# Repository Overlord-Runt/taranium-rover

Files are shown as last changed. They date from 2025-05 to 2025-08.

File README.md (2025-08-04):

# Taranium Rover
Made By Overlord Runt // Taran The Idiot

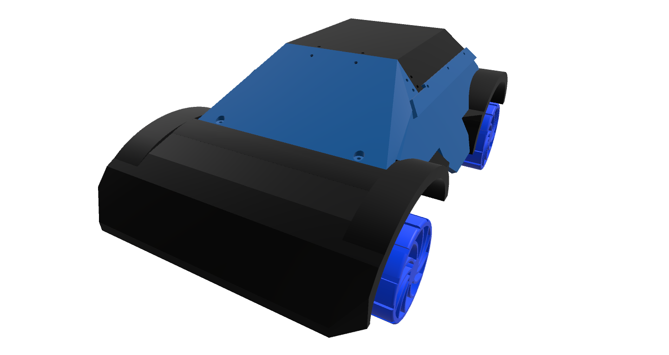
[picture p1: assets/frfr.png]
dksjfksd


## Taranium Rover
This is an RC car I made for Hack Club's [Highway](https://highway.hackclub.com). It has a 4WD system and can turn with all 4 wheels. It uses ESP32 and ESPNow to communicate between the car and the controller

## The Car

dsf

### CAD
Majority of this project was getting the cadding of all the different parts done. This isnt what normal custom RC Cars look like and thats because everyone uses the exact same optimal design but I want to make and design something myself. idrc about the "optimal way" cuz where is the fun in that.

This thing is really big so you need like a lot of plates if you want to build it. Roughly about 6 plates and 40 hours of non stop printing.

It uses a crap ton of M3 screws and heatsets, so make sure you stock up on those

### Engineering
So bunch of enginnering went into this design. First the turning system. the 2 front wheels turn separately to allow for differential steering and reduced drag. It also allows me to use weaker and smaller 9g servos that are able to turn one wheel, but not 2.\
It used steel dowels to hold the pieces together and to ensure minimal friction between parts(make it turn stronger)

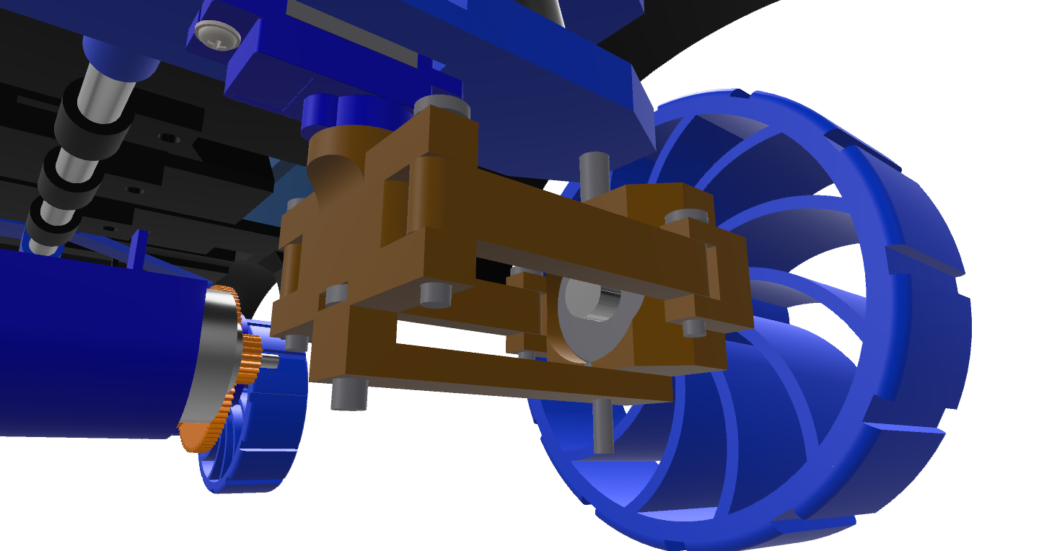
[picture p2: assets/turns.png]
fgd


The bottom piece is there for stability and to make sure the wheel mount doesnt collapse.\
The suspensions are a bunch of high strendth springs that help distribute the weight of the whole car evenly through the wheels and absorb large bumps.\
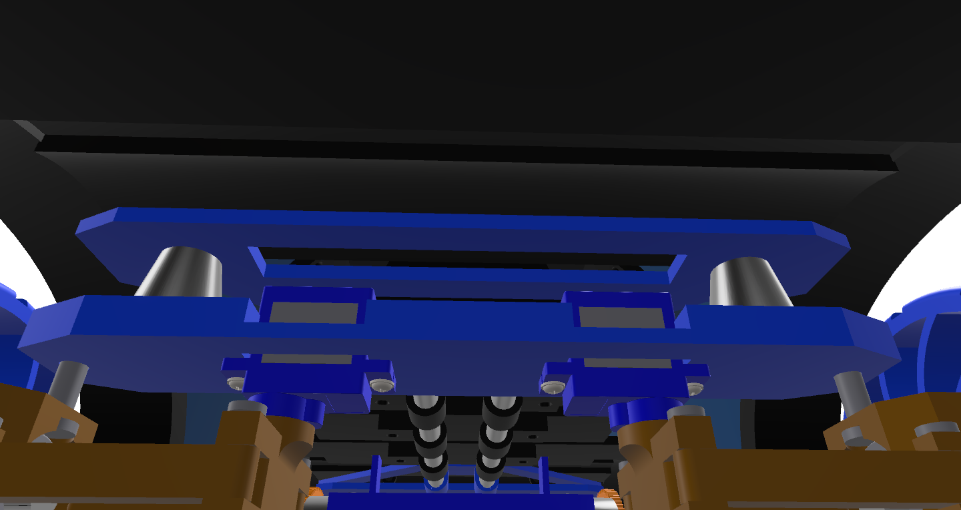
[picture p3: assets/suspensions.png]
dafs
\
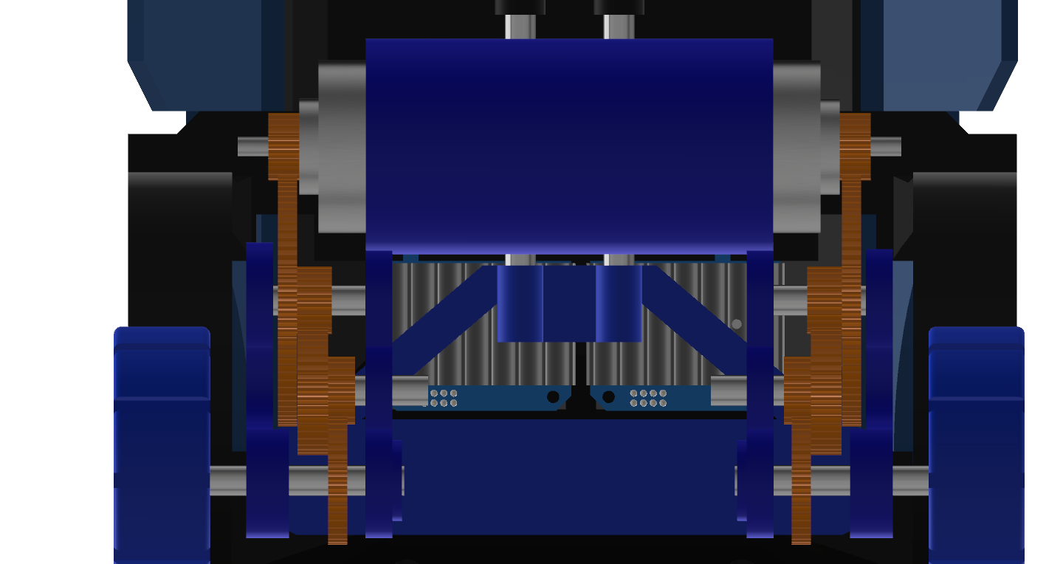
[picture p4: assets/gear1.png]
dfsdf


The gear system uses a 16:1 gear down from the 12 000 rpm motor to give a 750 rpm spin under no load with roughly 6-10 Kgcm torque. under load it will have about 4-500 rpm and go about 1m/s. I use a large amount of bearings and steel rods in this design. For assembly, use a grinder to chop the steel rods into all the different lengths needed. You can refer to Full-Build.step in the CAD folder to see how everything is put together.

### PCB / Wiring Diagrams
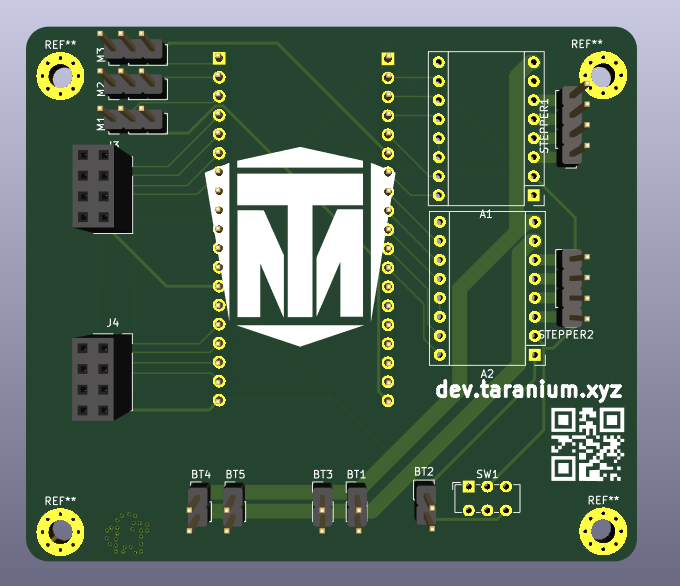
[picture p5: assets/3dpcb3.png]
sda


The PCB didnt really take too long but I did have to make many different revisions to get here that did end up taking a lot of time.\
I wanted this to be somewhat of a universal mainboard that could be used in multiple use cases. Which is why I included space for stepper motor drivers. specifically the A4988. as well as 3 places for servos

The PCB features 2 BTS7960 motor drivers. They have 8 pins that connect to the boards(mounted externally). The mainboard also has space to use A4988 stepper motor drivers if you wish to swap out the 775s for stepper motors. 

I didnt have a footprint for the esp32 board that I am using so I just used 2 header pins and separated them the distance that it said on the datasheet.

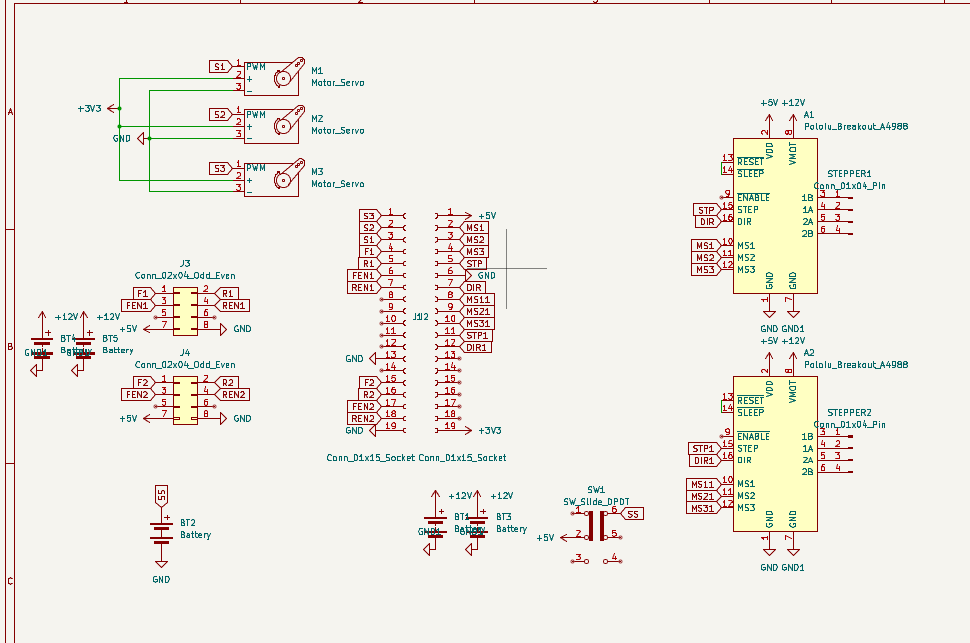
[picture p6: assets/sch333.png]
asd


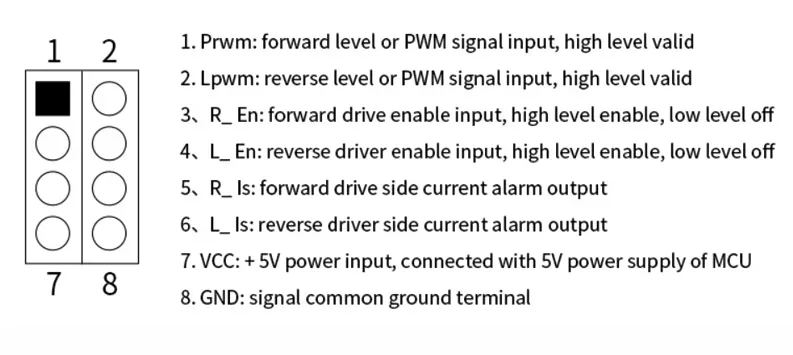
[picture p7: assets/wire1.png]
fadsf


this is the pinout for the Motor driver. it mathces that on the pcb so its an easy connection there

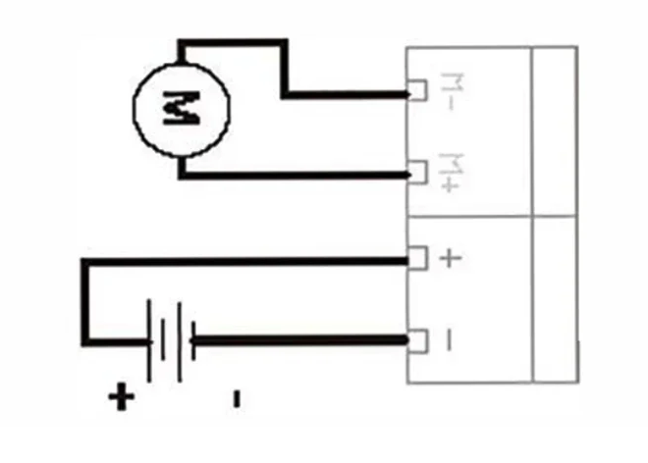
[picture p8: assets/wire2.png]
sdgfgsg


This is how you connect the motor driver to the battery and to the motor.

## The Controller
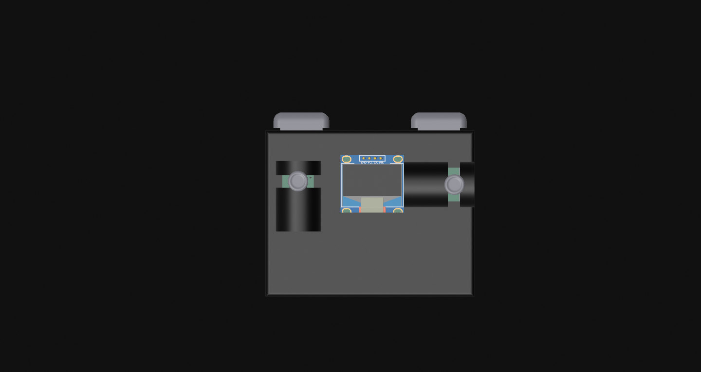
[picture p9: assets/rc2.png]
sdfs

### CAD
The controller was fairly easy to cad. it uses M3 screws to hold itself together.

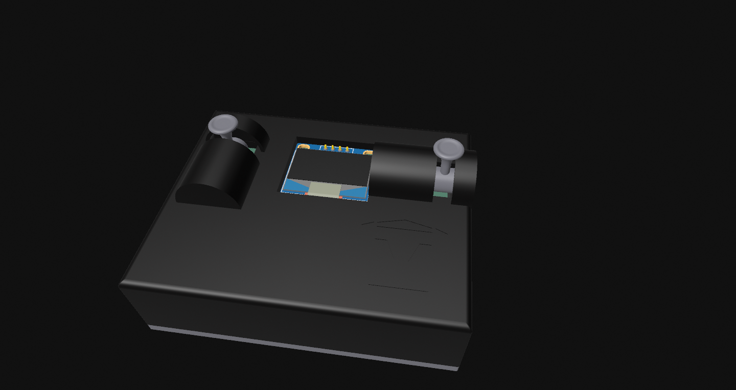
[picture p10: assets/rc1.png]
fs


The triggers are just extensions to the buttons with a small indent to act as a stabiliser

The joysticks/encoder rods are cool in that I didn't use the revolve tool to make them. just a bunch of extrusions, drafts, and fillets.

Then in order to make it actually buildable, i chopped off the end and added a dowel

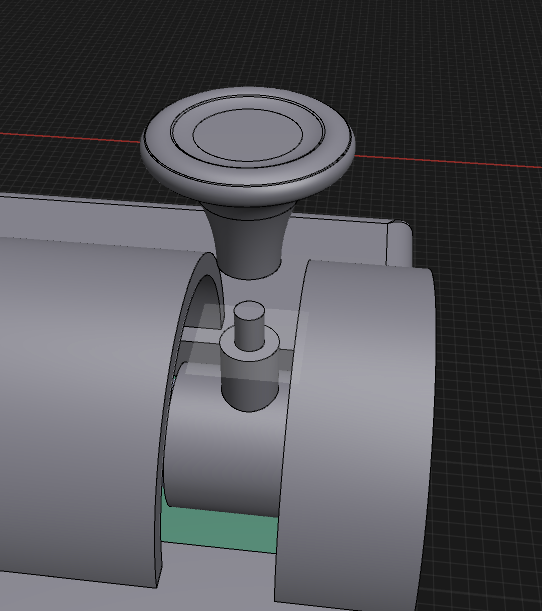
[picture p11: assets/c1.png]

### PCB
For the pcb I wanted to keep it basic. So 2 encoders. One for speed, other for turning. then 2 buttons. one to reverse, other for anything else you might wanna add in the future.\
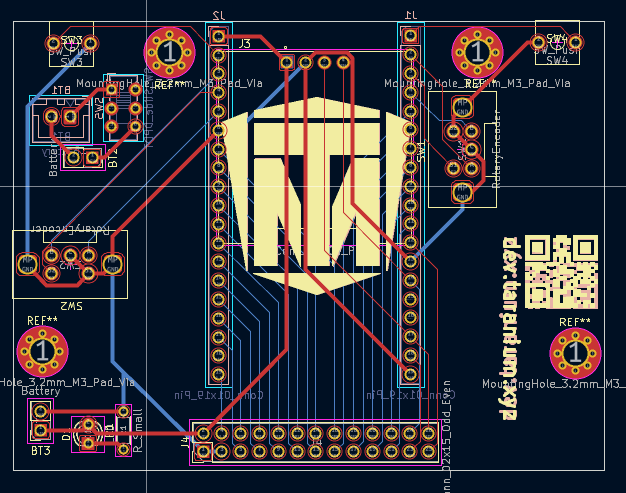
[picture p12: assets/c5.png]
\
Its a cool design if you ask me and it does its job.\
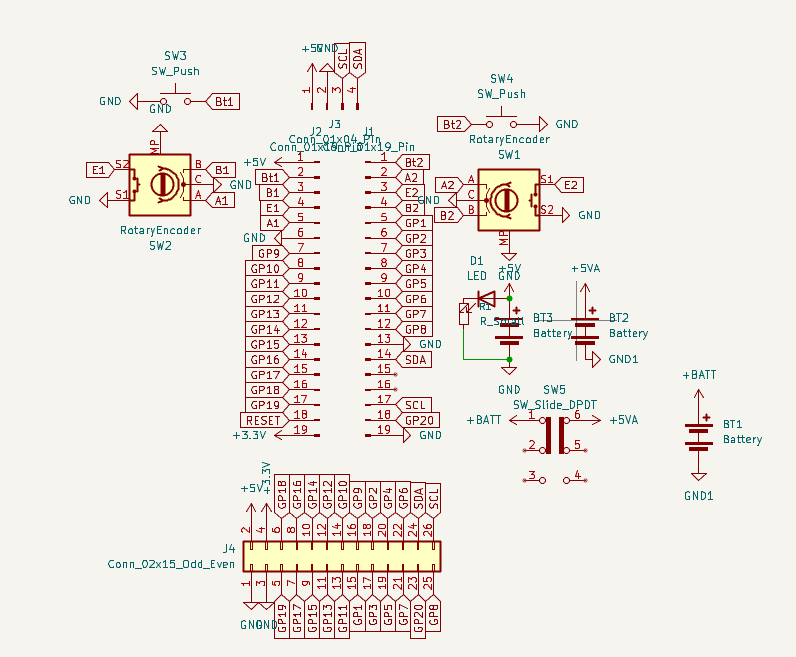
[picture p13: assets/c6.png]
sdad


## Firmware

uses espnow and you can find the firmware in the firmware folders. the names should tell you all you need to knwo about which on goes to which but for those who are a little slow, controller.ino flashes to the controller and mainboard.ino flashes to the mainboard

## How To Build

1. Print out all parts
2. Insert heatsets into all parts
3. Solder circuit boards as shown in schematics
4. assemble internal structures such as the turning system
5. Slide connectors onto rods then use rods to connect 2 internals sides
6. Attach chasis frames beginning with the parts that connect to the frame.
7. Flash esp with code
8. mount pcb of top panel
9. insert battery and sercure it down with screws
10. screw on top panels
11. flash controller with code
12. solder pcb
13. attach first part of the sticks to encoders
14. mount pcb to case
15. attach second part of sticks to encoders and use super glue or hot glue to hold it down
16. screw back panel
17. play enjoy.

If i forgot something I will add it on when I build

## BOM

|Name|QTY|Cost(AUD)|Cost(USD)|Link|
|----|---|---|---|----|
|3s 2.2AH LiPo|1|$47.19||[LINK](https://www.amazon.com.au/gp/product/B09NXM2DW4/ref=sw_img_1?smid=A3S3YJCXW342CA&psc=1)|
|ESP32 Dev Board|2|$7.39||[LINK](https://www.aliexpress.com/item/1005008499671222.html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)|
|Buck Converter|1|$1.47||[LINK](https://www.aliexpress.com/item/1005006365697021.html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)|
|Steel Rods|1|$13.59||[LINK](https://www.aliexpress.com/item/1005005041338002.html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)|
|775 12V DC Motor|2|$31.40|20.2|[LINK](https://www.aliexpress.com/item/1005006573459459.html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)|
|BTS7960 Motor Driver|2|$15.00|9.65|[LINK](https://www.aliexpress.com/item/1005007091280016.html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)|
|Header Pins|1|$2.54||[LINK](https://www.aliexpress.com/item/1005006034877497.html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)|
|Servo Motor 5V|2|$4.69||[LINK](https://www.aliexpress.com/item/1005006572297006.html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)|
|M3x10mm Screws||$2.82||[LINK](https://www.aliexpress.com/item/32810852732.html?spm=a2g0o.order_list.order_list_main.28.74441802cg1DM1)|
|M3x16mm Screws||$3.43||[LINK](https://www.aliexpress.com/item/32810852732.html?spm=a2g0o.order_list.order_list_main.28.74441802cg1DM1)|
|M3x6mm Screws||$2.29||[LINK](https://www.aliexpress.com/item/32810852732.html?spm=a2g0o.order_list.order_list_main.28.74441802cg1DM1)|
|M3D5L6 Heatsets|45|$3.82||[LINK](https://www.aliexpress.com/item/1005003582355741.html?spm=a2g0o.order_list.order_list_main.45.21221802z3BMxP)|
|M3 Steel Dowels 20mm|4|$2.47||[LINK](https://www.aliexpress.com/item/1005003990055624.html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)|
|M3 Steel Dowels 12mm|2|$2.41||[LINK](https://www.aliexpress.com/item/1005003990055624.html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)|
|M4 Steel Dowels 12mm|2|$2.47||[LINK](https://www.aliexpress.com/item/1005003990055624.html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)|
|M5 Steel Dowels 25mm|2|$3.16||[LINK](https://www.aliexpress.com/item/1005003990055624.html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)|
|Car Mainboard|1|9.18|$6.90|JLCPCB|
|Controller Board|1|15.1|$9.87|JLCPCB|
|3d Printed parts||||I aint counting how many there are|
|LiPo Balance Charger|1|$23.95||[LINK](https://www.amazon.com.au/Jinming-Battery-Balance-Charger-Blaster/dp/B07JDG4D8W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)|
|Horizontal Rotary Encoder|2|$4.90||[LINK](https://www.aliexpress.com/item/1005006128388016.html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)|
|T-plug connector|1|$2.61||[LINK](https://www.aliexpress.com/item/4001212535096.html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)|
|10 gauge wire|2m|$15.45||[LINK](https://www.aliexpress.com/item/1005007759043423.html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)|
|3.7V lipo|1|$14.99||[LINK](https://www.amazon.com.au/gp/product/B09R7F1VV5/ref=sw_img_1?smid=A12788XRWB37UE&th=1)|
|XH 2.54 Male connector|1|$1.79||[LINK](https://www.aliexpress.com/item/1005007460897865.html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)|
|6mm switch|2|$2.89||[LINK](https://www.aliexpress.com/item/1005004971266223.html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)|
|Hardened Springs|4|||sourced from my dad|
|1kg PLA|1||||
|1kg PETG|1||||
|Boost Converter|1|$4.83||[LINK](https://www.aliexpress.com/item/1005008447199869.html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)|
|SSD1306 128x64 OLED Display|1|$4.20||[LINK](https://www.aliexpress.com/item/1005009243034318.html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)|
|TOTAL||$246.03|$161.03||

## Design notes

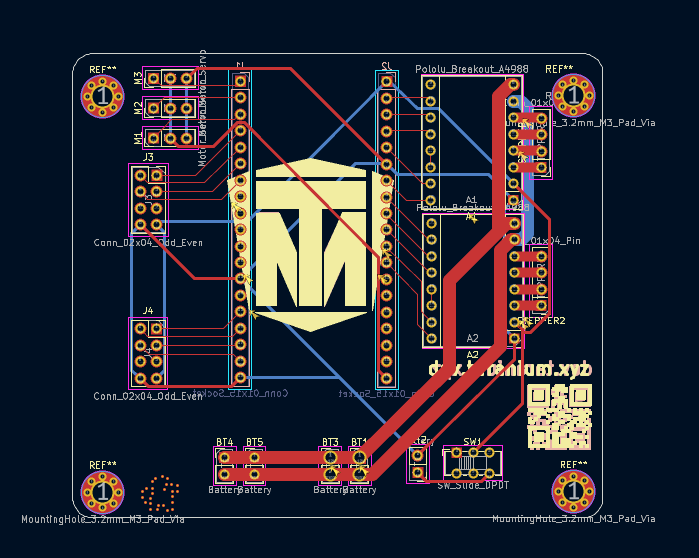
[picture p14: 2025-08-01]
assets/pcb333.png

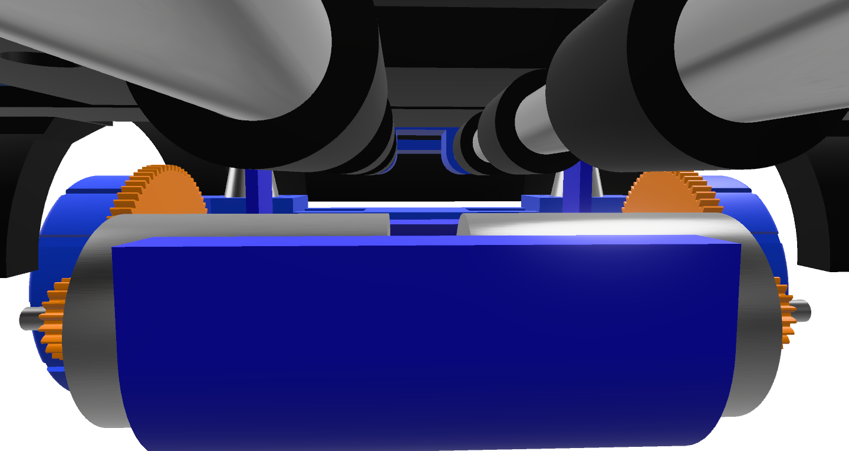
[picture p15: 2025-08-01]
assets/mots.png

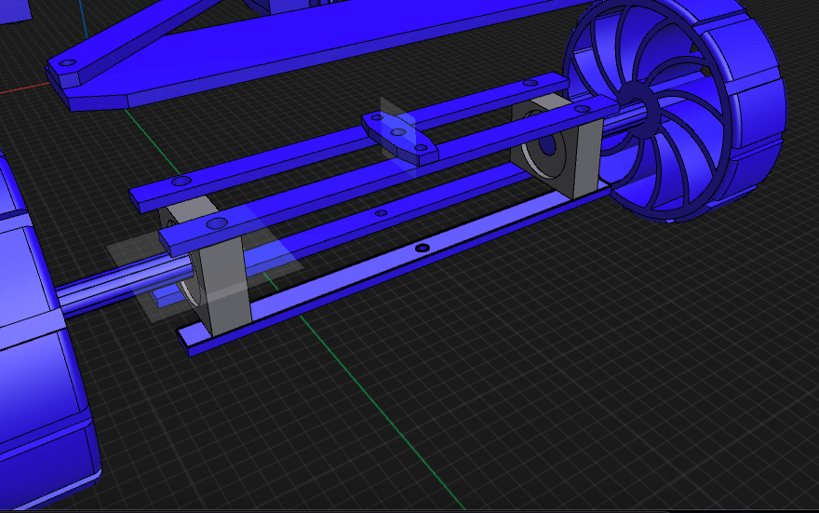
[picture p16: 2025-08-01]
assets/turn2.png

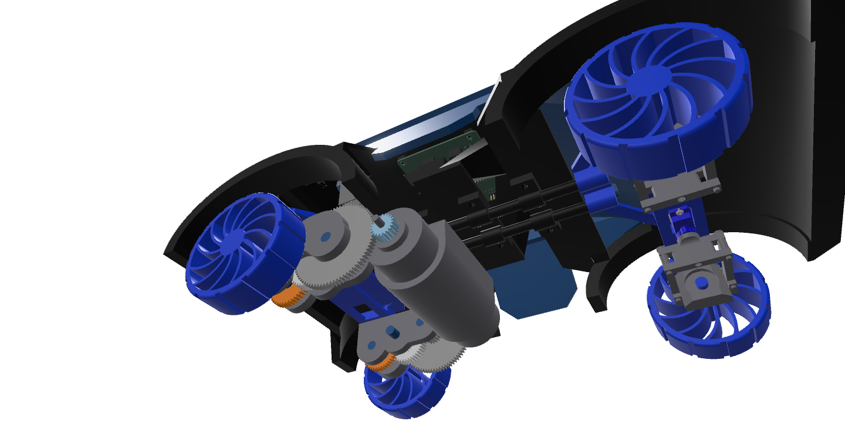
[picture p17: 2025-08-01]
assets/internals.png

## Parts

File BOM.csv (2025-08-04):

Name | QTY | Cost(AUD) | Cost(USD) | Link
3s 2.2AH LiPo | 1 | $47.19 |  | https://www.amazon.com.au/gp/product/B09NXM2DW4/ref=sw_img_1?smid=A3S3YJCXW342CA&psc=1
ESP32 Dev Board | 2 | $7.39 |  | https://www.aliexpress.com/item/1005008499671222.html?mp=1
Buck Converter | 1 | $1.47 |  | https://www.aliexpress.com/item/1005006365697021.html?mp=1
Steel Rods | 1 | $13.59 |  | https://www.aliexpress.com/item/1005005041338002.html?mp=1
775 12V DC Motor | 2 | $31.40 | 20.2 | https://www.aliexpress.com/item/1005006573459459.html?mp=1
BTS7960 Motor Driver | 2 | $15.00 | 9.65 | https://www.aliexpress.com/item/1005007091280016.html?mp=1
Header Pins | 1 | $2.54 |  | https://www.aliexpress.com/item/1005006034877497.html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
Servo Motor 5V | 2 | $4.69 |  | https://www.aliexpress.com/item/1005006572297006.html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
M3x10mm Screws |  | $2.82 |  | https://www.aliexpress.com/item/32810852732.html
M3x16mm Screws |  | $3.43 |  | https://www.aliexpress.com/item/32810852732.html
M3x6mm Screws |  | $2.29 |  | https://www.aliexpress.com/item/32810852732.html
M3D5L6 Heatsets | 45 | $3.82 |  | https://www.aliexpress.com/item/1005003582355741.html
M3 Steel Dowels 20mm | 4 | $2.47 |  | https://www.aliexpress.com/item/1005003990055624.html?mp=1
M3 Steel Dowels 12mm | 2 | $2.41 |  | https://www.aliexpress.com/item/1005003990055624.html?mp=1
M4 Steel Dowels 12mm | 2 | $2.47 |  | https://www.aliexpress.com/item/1005003990055624.html?mp=1
M5 Steel Dowels 25mm | 2 | $3.16 |  | https://www.aliexpress.com/item/1005003990055624.html?mp=1
Car Mainboard | 1 | 9.18 | $6.90 | JLCPCB
Controller Board | 1 | 15.1 | $9.87 | JLCPCB
3d Printed parts |  |  |  | I aint counting how many there are
LiPo Balance Charger | 1 | $23.95 |  | https://www.amazon.com.au/Jinming-Battery-Balance-Charger-Blaster/dp/B07JDG4D8W
Horizontal Rotary Encoder | 2 | $4.90 |  | https://www.aliexpress.com/item/1005006128388016.html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
T-plug connector | 1 | $2.61 |  | https://www.aliexpress.com/item/4001212535096.html?mp=1
10 gauge wire | 2m | $15.45 |  | https://www.aliexpress.com/item/1005007759043423.html?mp=1
3.7V lipo | 1 | $14.99 |  | https://www.amazon.com.au/gp/product/B09R7F1VV5/ref=sw_img_1?smid=A12788XRWB37UE&th=1
XH 2.54 Male connector | 1 | $1.79 |  | https://www.aliexpress.com/item/1005007460897865.html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
6mm switch | 2 | $2.89 |  | https://www.aliexpress.com/item/1005004971266223.html?mp=1
Hardened Springs | 4 |  |  | sourced from my dad
1kg PLA | 1
1kg PETG | 1 |  |  | Converter | 1 | $4.83 | https://www.aliexpress.com/item/1005008447199869.html?mp=1
SSD1306 128x64 OLED Display | 1 | $4.20 |  | https://www.aliexpress.com/item/1005009243034318.html?mp=1
TOTAL |  | $246.03 | $161.03

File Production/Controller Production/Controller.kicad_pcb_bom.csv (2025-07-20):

Designator | Quantity | Value | Footprint | Package | MPN | DNP | Mount_Type | Description | Sim.Pins
BT1 | 1 | Battery | JST_XH_B2B-XH-A_1x02_P2.50mm_Vertical |  |  |  | tht | Multiple-cell battery
BT2, BT3 | 2 | Battery | PinSocket_1x02_P2.54mm_Vertical |  |  |  | tht | Multiple-cell battery
D1 | 1 | LED | LED_D3.0mm |  |  |  | tht | Light emitting diode | 1=K 2=A
J1, J2 | 2 | Conn_01x19_Pin | PinSocket_1x19_P2.54mm_Vertical |  |  |  | tht | Generic connector, single row, 01x19, script generated
J3 | 1 | Conn_01x04_Pin | MODULE_DM-OLED096-636 |  |  |  | tht | Generic connector, single row, 01x04, script generated
J4 | 1 | Conn_02x15_Odd_Even | PinHeader_2x13_P2.54mm_Vertical |  |  |  | tht | Generic connector, double row, 02x13, odd/even pin numbering scheme (row 1 odd numbers, row 2 even numbers), script generated (kicad-library-utils/schlib/autogen/connector/)
R1 | 1 | R_Small | R_Axial_DIN0204_L3.6mm_D1.6mm_P5.08mm_Horizontal |  |  |  | tht | Resistor, small symbol
SW1, SW2 | 2 | RotaryEncoder | EC11-Horizontal |  |  |  | tht | Rotary encoder, dual channel, incremental quadrate outputs, with switch and MP Pin
SW3, SW4 | 2 | SW_Push | Button-6mm-2pin-tht |  |  |  | smt | Push button switch, generic, two pins
SW5 | 1 | SW_Slide_DPDT | SW_E-Switch_EG1271_SPDT |  |  |  | tht | Slide Switch, dual pole double throw

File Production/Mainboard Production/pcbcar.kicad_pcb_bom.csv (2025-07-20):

Designator | Quantity | Value | Footprint | Package | MPN | DNP | Mount_Type | Description
A1, A2 | 2 | Pololu_Breakout_A4988 | Pololu_Breakout-16_15.2x20.3mm |  |  |  | tht | Pololu Breakout Board, Stepper Driver A4988
BT1, BT2, BT3 | 3 | Battery | PinHeader_1x02_P2.54mm_Vertical |  |  |  | tht | Multiple-cell battery
DCM1, DCM2, DCM3, DCM4, DCM5, DCM6 | 6 | Conn_01x02_Pin | PinHeader_1x02_P2.54mm_Vertical |  |  |  | tht | Generic connector, single row, 01x02, script generated
J1, J2 | 2 | Conn_01x15_Socket | PinHeader_1x19_P2.54mm_Vertical |  |  |  | tht | Generic connector, single row, 01x19, script generated
M1, M2, M3 | 3 | Motor_Servo | PinHeader_1x03_P2.54mm_Vertical |  |  |  | tht | Servo Motor (Futaba, HiTec, JR connector)
MD1, MD2, MD3 | 3 | ~ | MODULE_ROB-14450 |  |  |  | tht
STEPPER1, STEPPER2 | 2 | Conn_01x04_Pin | PinHeader_1x04_P2.54mm_Vertical |  |  |  | tht | Generic connector, single row, 01x04, script generated
SW1 | 1 | SW_Slide_DPDT | SW_E-Switch_EG1271_SPDT |  |  |  | tht | Slide Switch, dual pole double throw

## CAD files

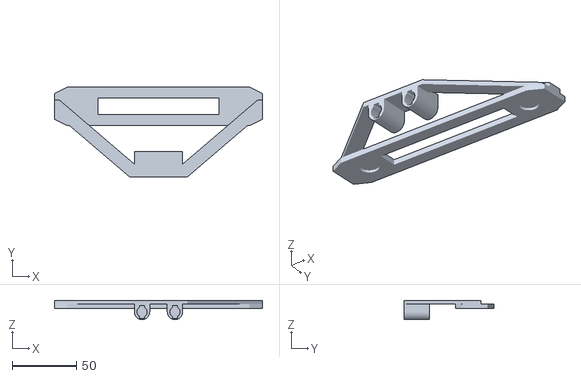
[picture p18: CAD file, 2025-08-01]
CAD/STLs/RC-Car_Assembly 1.step (1).stl
162.0 x 70.0 x 15.0

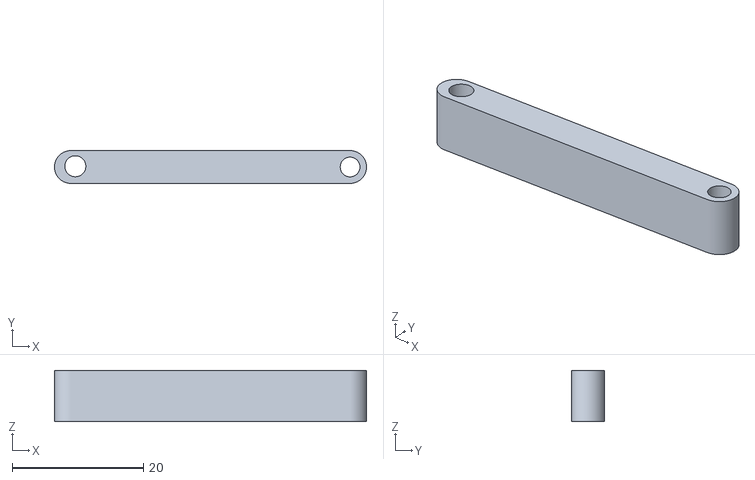
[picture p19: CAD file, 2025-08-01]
CAD/STLs/RC-Car_Body 94.stl
47.5 x 5.00 x 7.80

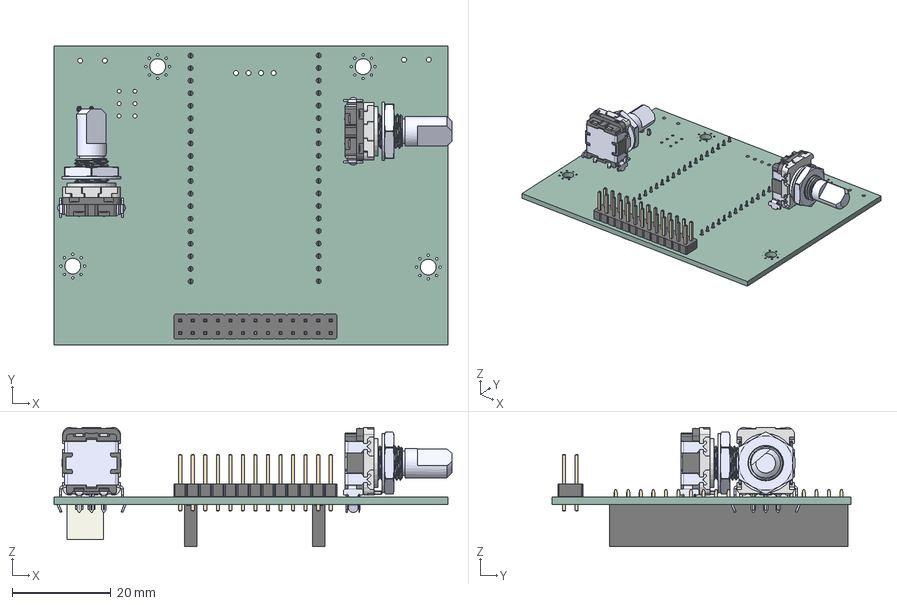
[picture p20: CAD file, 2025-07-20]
Controller/Controller.step
80.6 x 60.6 x 24.2 mm
EC11B-Shaft-F x 2
EC11B-HousingSW-horiz x 2
PinHeader_2x13_P2.54mm_Vertical
PinSocket_1x19_P2.54mm_Vertical x 2
JST_XH_B2B-XH-A_1x02_P2.50mm_Vertical
Controller_PCB

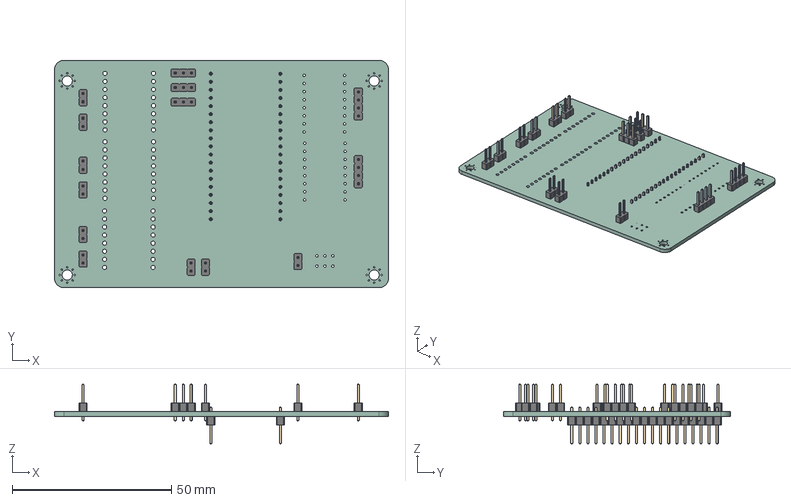
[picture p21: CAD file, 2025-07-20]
Mainboard/pcbcar.step
105.0 x 71.5 x 18.8 mm
PinHeader_1x02_P2.54mm_Vertical x 9
PinHeader_1x04_P2.54mm_Vertical x 2
PinHeader_1x03_P2.54mm_Vertical x 3
PinHeader_1x19_P2.54mm_Vertical x 2
pcbcar_PCB

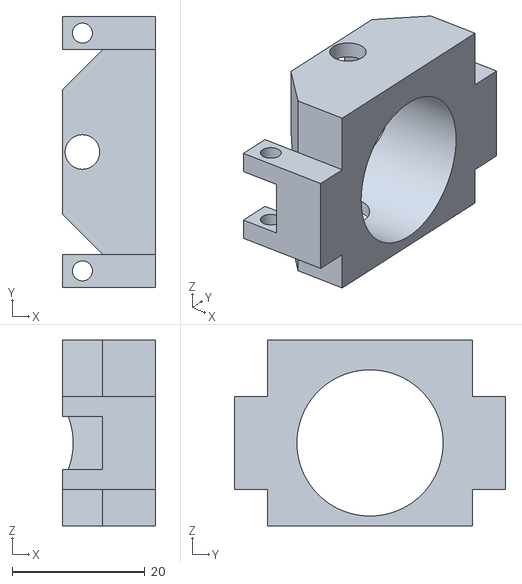
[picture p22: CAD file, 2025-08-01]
CAD/STLs/RC-Car_Body 59* (2).stl
14.0 x 40.8 x 28.0

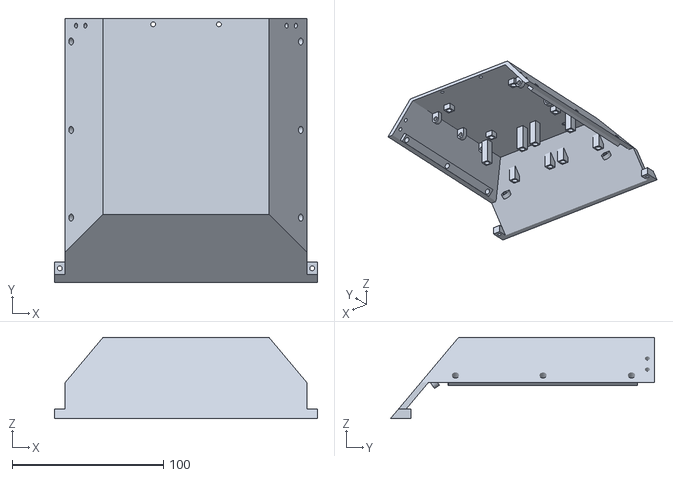
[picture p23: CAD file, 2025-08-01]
CAD/STLs/RC-Car_Body 228*5.stl
174.0 x 174.9 x 53.9

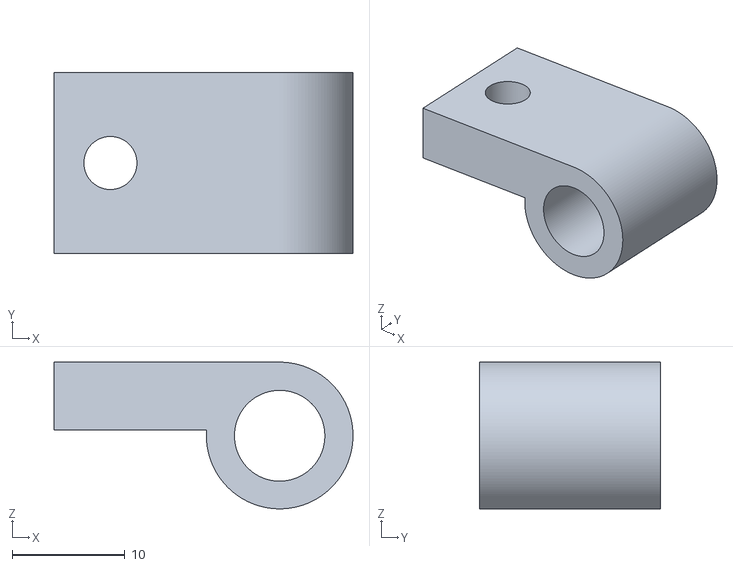
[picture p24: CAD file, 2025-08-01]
CAD/STLs/RC-Car_Body 23 (1) 2.stl
26.5 x 16.0 x 13.0

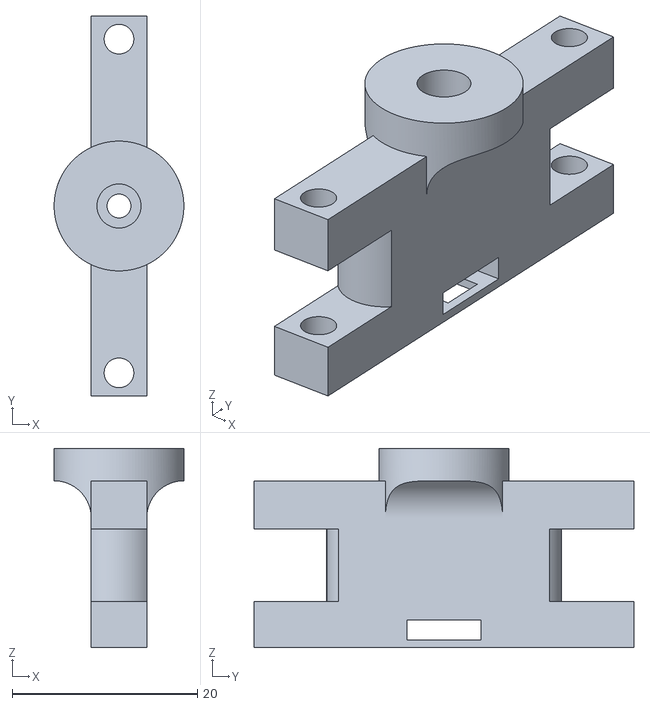
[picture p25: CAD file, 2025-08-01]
CAD/STLs/RC-Car_Body 92 (1).stl
14.0 x 41.0 x 21.5

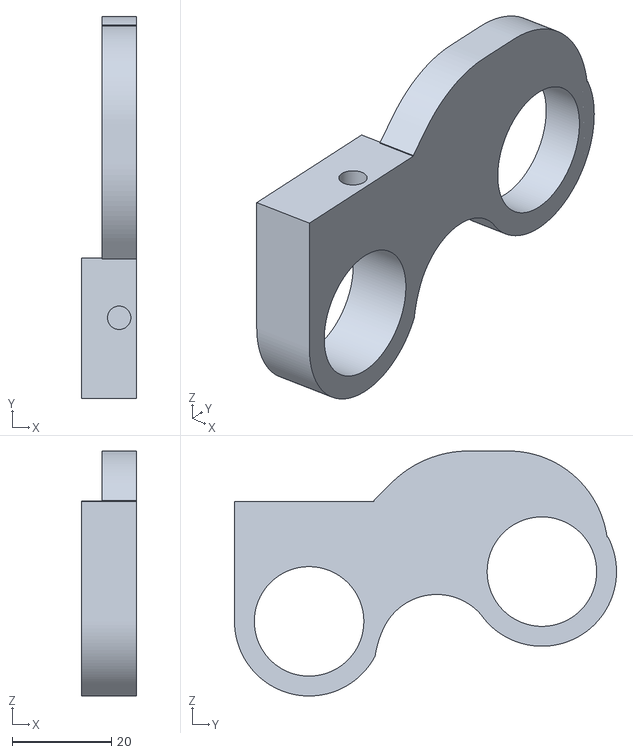
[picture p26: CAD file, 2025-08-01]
CAD/STLs/RC-Car_Body 63 (8)*2.stl
11.1 x 76.8 x 49.3

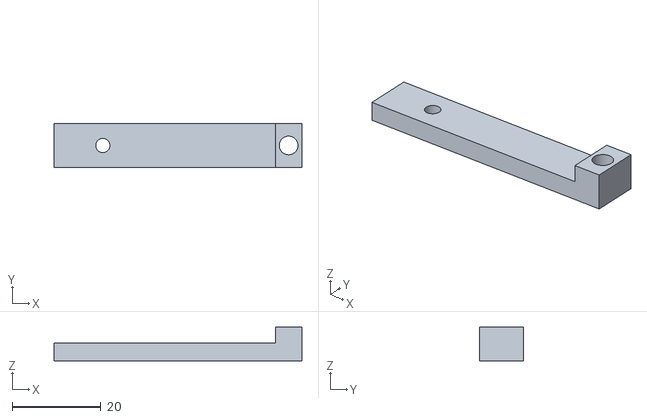
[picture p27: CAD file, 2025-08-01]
CAD/STLs/RC-Car_Body 219.stl
55.8 x 10.0 x 7.60

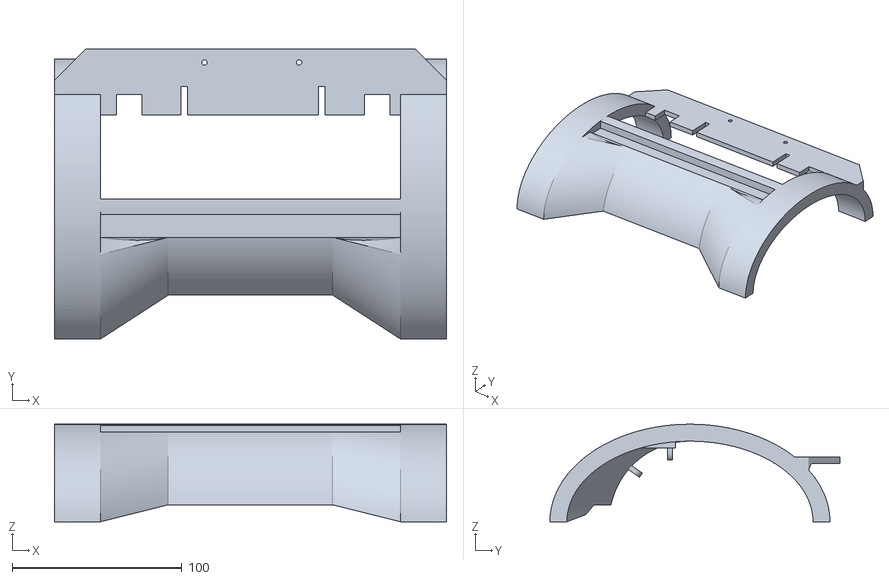
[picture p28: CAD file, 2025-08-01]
CAD/STLs/RC-Car_Body 53 (1).stl
230.9 x 171.0 x 57.5

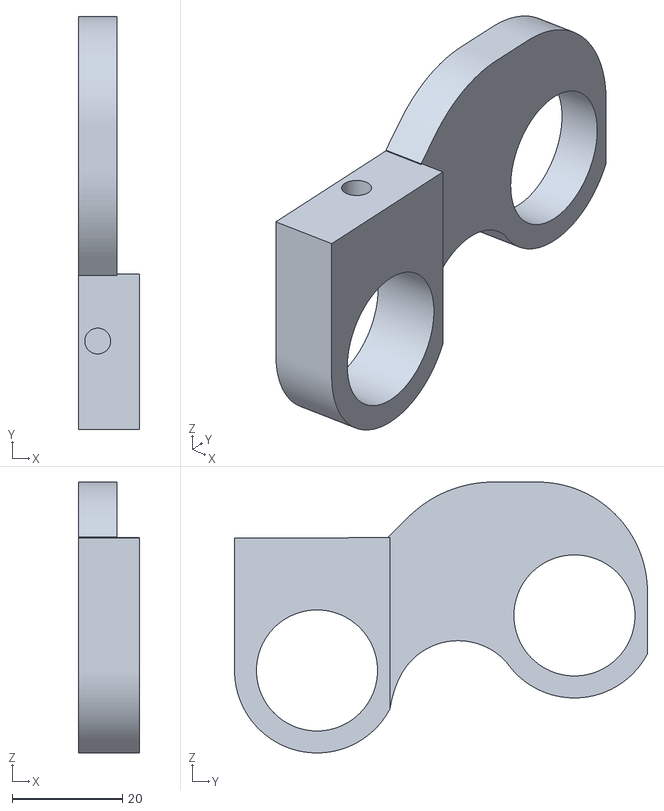
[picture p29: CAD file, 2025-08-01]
CAD/STLs/RC-Car_Body 64 (5).stl
11.1 x 75.1 x 49.3

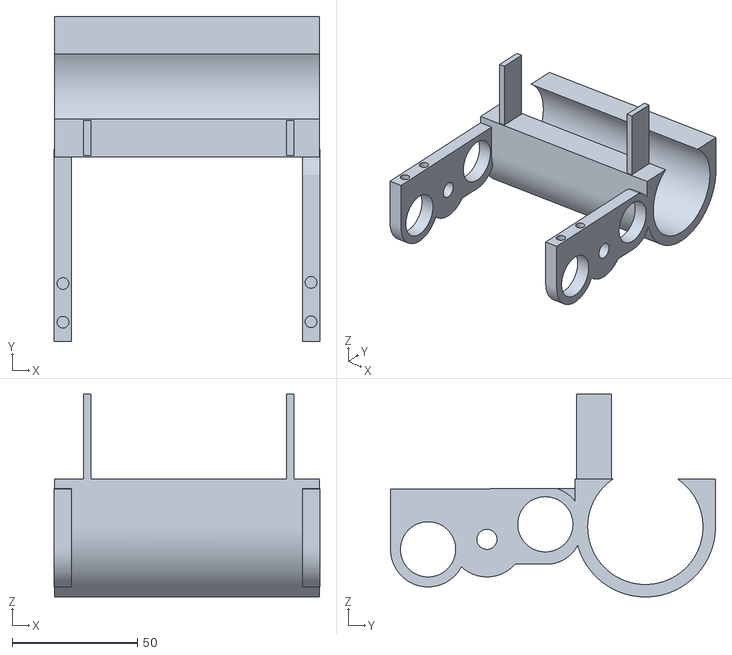
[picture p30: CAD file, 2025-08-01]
CAD/STLs/RC-Car_Body 64 (3).stl
106.0 x 129.7 x 81.0

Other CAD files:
CAD/STLs/RC-Car_Body 23 (1) 3.stl
CAD/STLs/RC-Car_Body 92 (2).stl
CAD/STLs/RC-Car_Body 93.stl
CAD/STLs/RC-Car_Body 23.stl
CAD/STLs/RC-Car_Body 59* (1).stl
CAD/STLs/RC-Car_Body 219 (1).stl
CAD/STLs/RC-Car_Body 23 (1).stl
CAD/STLs/RC-Car_Body 23 (2) 2.stl
CAD/STLs/RC-Car_Body 23 (2).stl
CAD/STLs/RC-Car_Body 53 (3).stl
CAD/STLs/RC-Car_Body 55 2.stl
CAD/STLs/RC-Car_Body 56 2.stl
CAD/STLs/RC-Car_Body 56.stl
CAD/STLs/RC-Car_Body 59.stl
CAD/STLs/RC-Car_Body 61 (1).stl
CAD/STLs/RC-Car_Body 61.stl
CAD/STLs/RC-Car_Body 93 (1).stl
CAD/STLs/RC-Car_Body 94 (1).stl

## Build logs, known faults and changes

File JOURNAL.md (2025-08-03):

---
title: "Taranium Rover"
author: "Taran The Idiot"
description: "An RC car"
created_at: "2025-05-15"
---

total time spent: 88 hours

## 15th of May

highway was just announced :D

Anyways I was coming up with a few project ideas when suddenly I thought: GUN\
But a gun is boring tbh. It just shoots and does weird stuff.\
So what could be better than a gun you may ask?\
A gun.... ON WHEELS.\
But what could be better than a gun on wheels?\
A REMOTE CONTROL GUN ON WHEELS.

You heard it here first folks. thats how we roll.

Anyways now its time for my suoer cool progress report\
*insert super cool name for the project report*\
I did some cadding today for like an hour or 2 and I made a wheel :D\
I also made some gears and mechanical stuff for the back tires.\
thats about it tbh.\
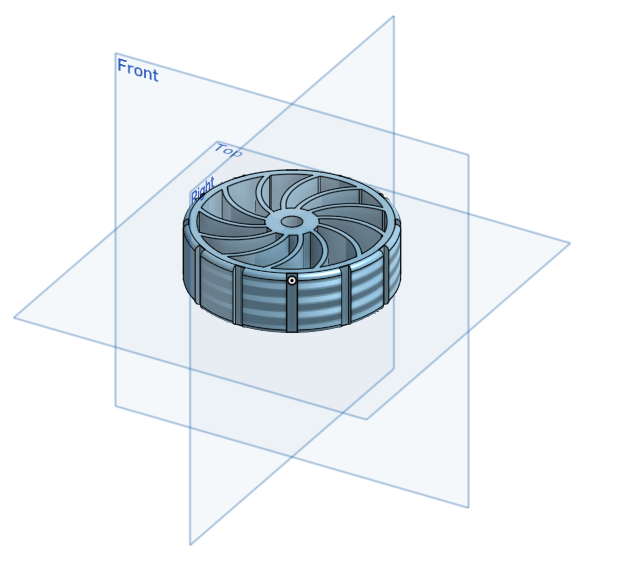
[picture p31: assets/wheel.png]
wheel
\
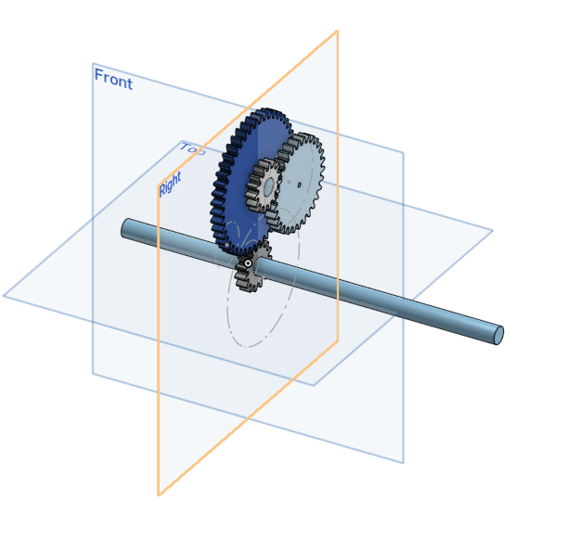
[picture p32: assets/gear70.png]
gear


Anyways time for a farewell my good friends, \
Until the next we meet.

Time spent: about an hour

## 16th of May

hello. I am writing this on the 17th cuz i forgot to do it yesterday.\
anyways I dibbled a bit in the cad but mainly started up with my pcb and electronics.

so I started doing pcb stuff. but I came across a problem.\
I dont want to buy and use a motor driver. but I need the dc motor to be able to move forwards and backwards.\
after a bit of thinking, i remembered an old school project where i did that but with a physical switch.\
now the question was, how do i make that into something i can turn on with gpio pins?

after a bunch of thinking and designs later, I reinvented the H bridge.\
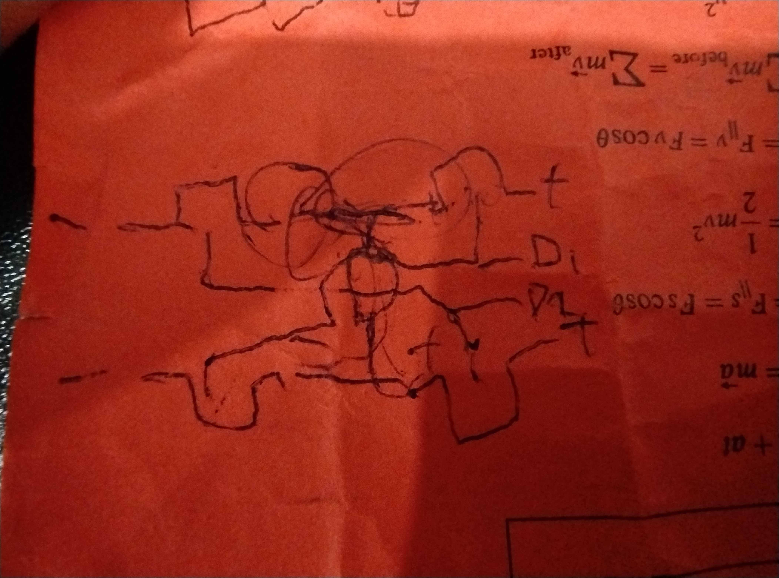
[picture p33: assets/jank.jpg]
h


after that i started work on the schematic and pcb and ended off the day looking like this:\
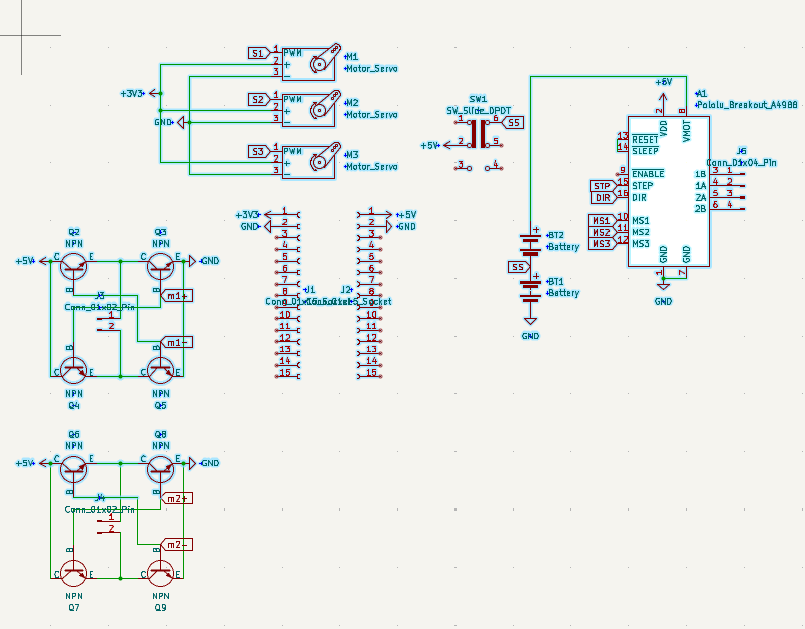
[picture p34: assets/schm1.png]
schm1
\
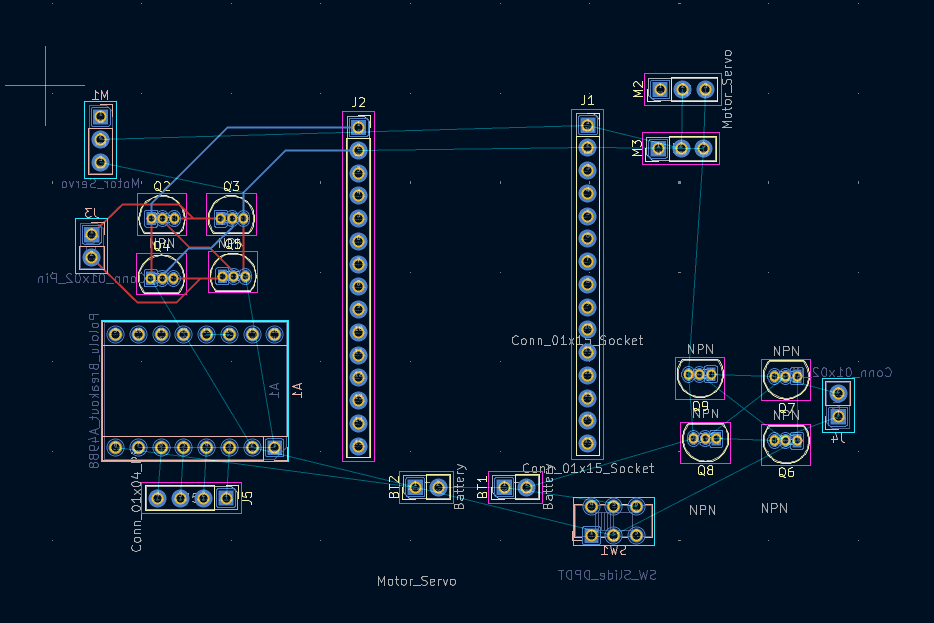
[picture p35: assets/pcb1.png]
pcb1


oh yeah i decided to use an esp32 as the mcu so i could use esp-now as the communication between it and the controller.

Time spend: 1-2 hours(I forgot but somewhere in that range)

## 17th of May

okay time for todays update. im gonna talk as if you have image references and then add the images in later cuz im not bothered rn tbh.\
if you can see images here then congrats, you came after i added images.

Okay so with my schematic i added a whole bunch of stuff like the stepper motor, more h-bridges, more servos, battery connectors, etc.\
also that weird stuff going on with my battery connectors is me trying to make both a 6V and 12V power supply come from 2 6V batteries.\
so the diodes limit the flow so it doesnt blow up on itself and the batteries are aranged so they are both in series and in parallel at the same time.

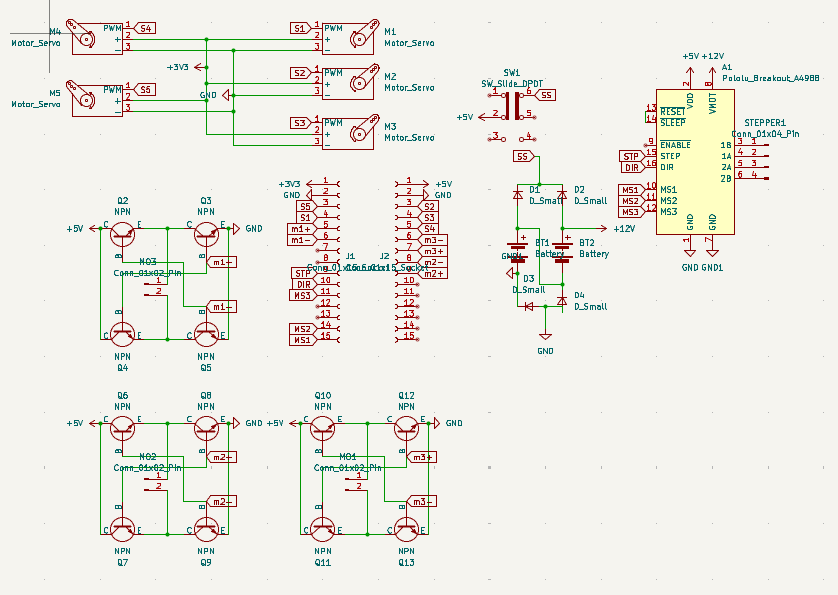
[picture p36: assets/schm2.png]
schem


I also added more h-bridges and servo spots than im actually gonna use\
the thought process is that if in the future i wanted to change up the functionality, then i could use those extra ones if needed. plus I had space anyways.

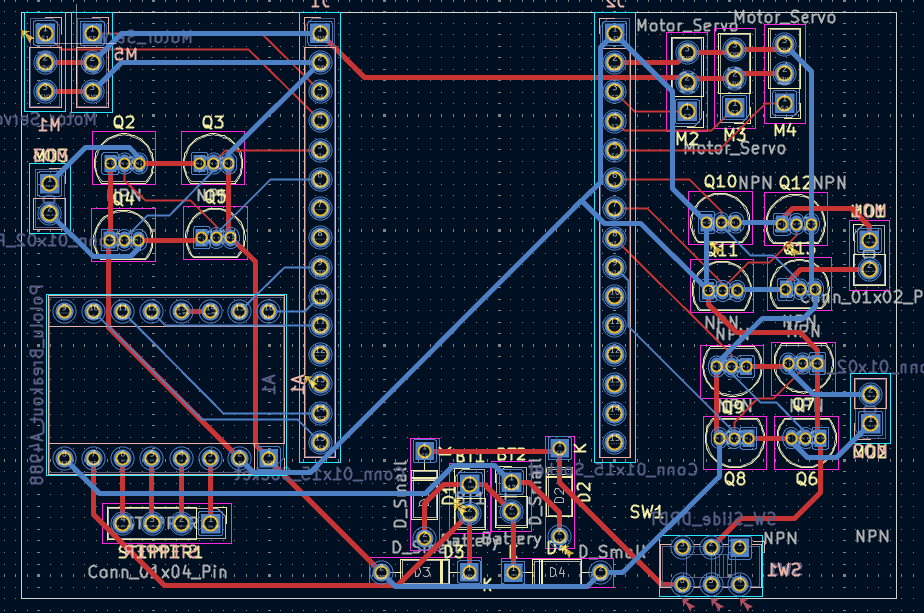
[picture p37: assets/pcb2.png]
pcb
\
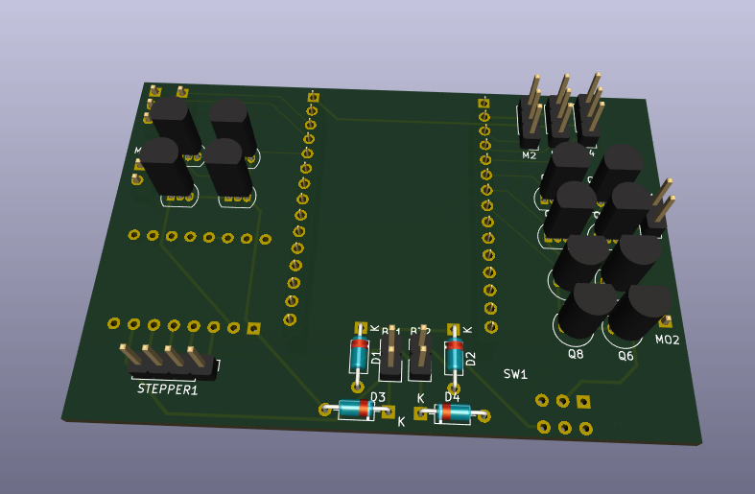
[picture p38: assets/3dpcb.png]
3d


tmrw im gonna probably gonna go and start on the internals cadding. but i need to do meth and physics hw first :(\
anyways bye

Time spent today: 5 hours

## 18th of May
### 1am
so i was looking into the esp input voltage and turn out it can handle a 12V input.\
but that diode mess was not for nothing. I still need it for my motors.\

UPDATE: im just gonna use a buck converter. I dont wanna gamble on my idea just to save $2

found a nice battery so gonna save the link here: https://www.amazon.com.au/cart/smart-wagon?newItems=af51fb0b-661d-4de9-b8e5-c46f956c932f,1&ref_=sw_refresh

Hours spent: 1

## 21st of May
I'm finally back

anyways I am in pain\
onshape sucks\
and linux literally doesnt have any better options.\
so until i get a new laptop, its gonna be incredibly slow production.

anyways what i did today:\
lots of cadding and stuff.\
made some ideas for suspensions\
got a lesson from my dad on how suspensions are stupidly harder to use\
settled on just hard connections\
now designing that stuff\
learnt how horrid onshape is for doing anything big of with lots of parts.

hours spent: 3

## 23rd of May

okay so i got sick yesterday and wasnt able to make an entry so im gonna summarise both days work today. 

So first some yap. In approximately 11 hours and 35 minutes, the kickoff call will start. thats fun and exciting.

Okay so onwards to what I did.\
Yesterday I worked a lot on my back half of the car and did quite a lot of work and got most of the interals done for the back half of the car. And today I finished up those internals and got them at an acceptable standard for me.

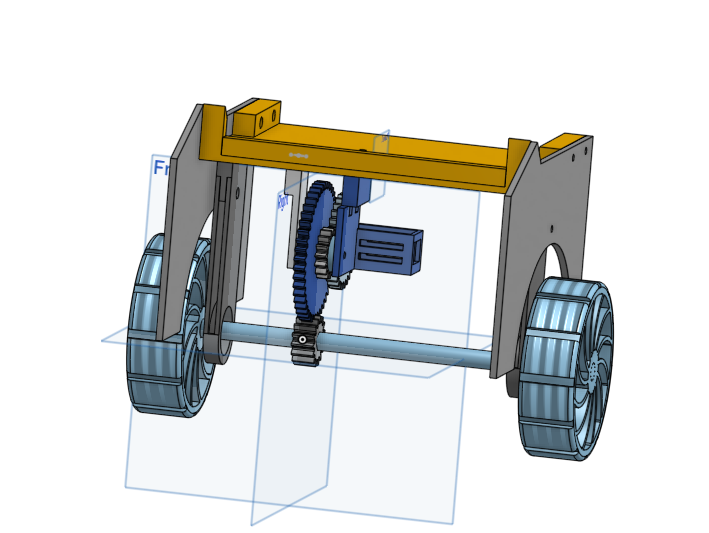
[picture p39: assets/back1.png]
\
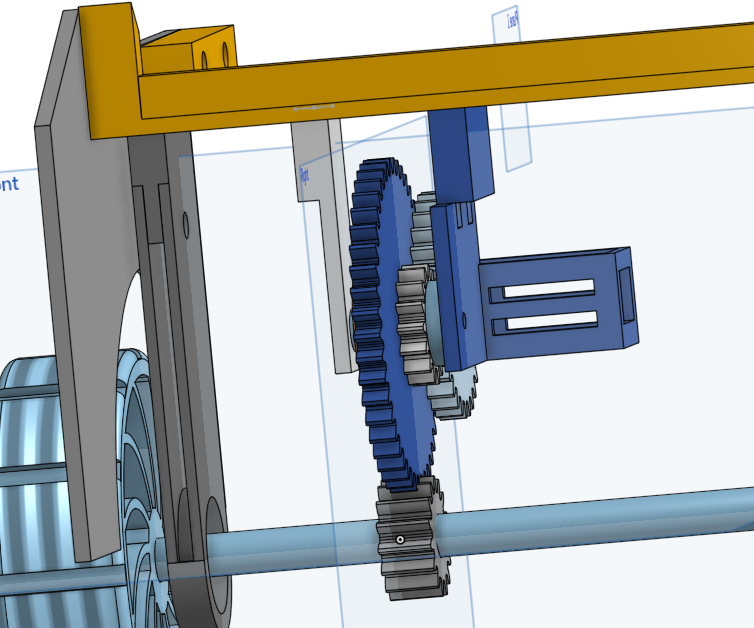
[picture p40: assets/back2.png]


I also got started on the gun mechanism and roughly mapped out 2 of the axis for my gun to move around with.

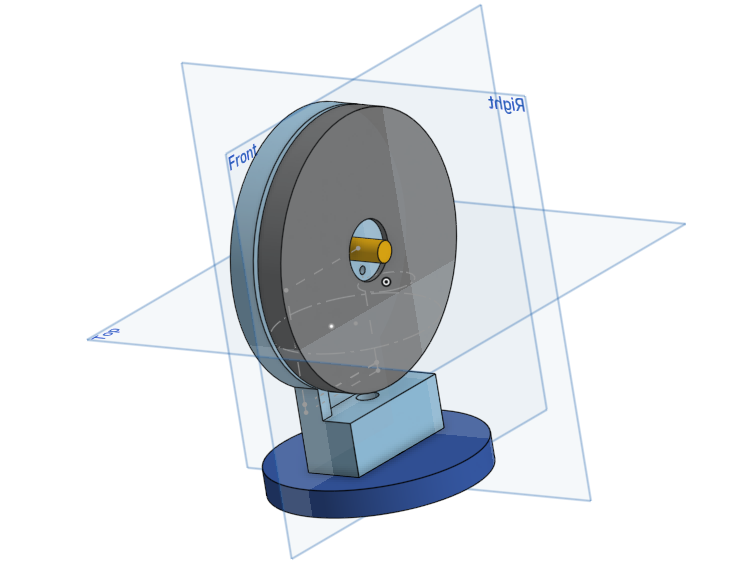
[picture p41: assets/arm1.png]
\
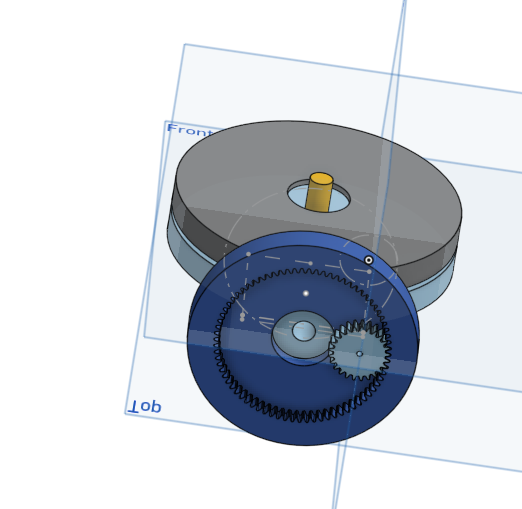
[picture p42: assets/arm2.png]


# THE PROBLEM

So due to australian gun laws, it is illegal to possess, make, or hold schematics of any weapon. Toy or not.\
Due to this, my entire plan of making a gun on top of an rc car is shut down.\
So what can i do to solve this?\
Its an rc car with a 4 axis robotic arm on top.\
Instead of a ranged weapon, its a close combat fighter. /j

anyways thats my idea now so I need to go back and make changes to my pcb and bom. I need to add another stepper motor to my pcb(this is gonna take a big battery)\
My plan for the arm is to have 3 bending points and one spinning point. the bottom bending point uses a stepper motor for extra strength and the top 2 and hand will use servos the hand might use a 5v motor though. (havent decided yet)

hours spent: 5

## 24th of May
so today was the call for highway and it was peak.

today i started part research and a pcb overhaul to accomodate for the extra motors needed in the arm. now the problems with this: I found out that the transistors i am using can only handle up to 100 mA when i need about 1A to drive the motor. so thats a big problem. Next problem: Im using 12V motors and most mosfets i looked at cant properly fuction with 12V and a 3.3V trigger and the ones that do are all smd parts which are impossible for me to work with.

so my plan rn is to just leave this until i find a solution and start working on something else.

time spent: 3 hours

## 4th of June

Im starting to work on this again and its pretty cool. I started on the arm since I am on a brain block on how to make the body.\
I made the hand part of the arm today.

For the hand, I used a worm gear(i think thats the name) with 4 prongs.

It started with a spur gear with a massive centre bore, Then I made 2 cuts from the centre out and got left with ~200-230 degrees of gear.\
I made a sketch for the prong to attach to the end of the gear and extruded it out both sides to make a prong. I then put a zigzag on the end of the prong and added a chamfer.

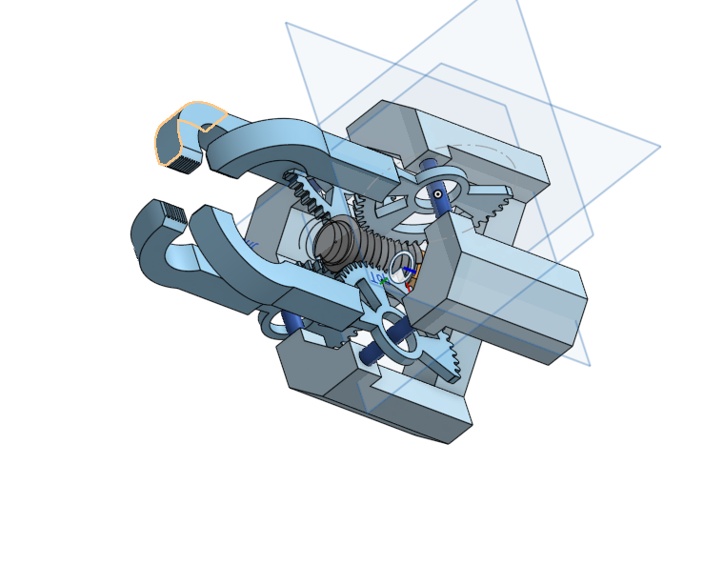
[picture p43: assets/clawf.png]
boo


I then spent an hour trying to learn how to make screws and made a centre screw for the hand.\
I then copied it 3 times around the screw to make it look like the picture above.

Next was the frame. This was the hardish part.\
I started by editing the prongs to add a centre hole for a bearing and put a rod through it\
Then I made corner frame parts by alligning the 4 prongs\
I also made some chamfers to make it look nice

Next was the motor holder, I extruded 4 corners and platformed around a rectangle that I made as a motor placeholder.\

Next i put a square to hold the 4 parts together with screws.

And that was my day.

Time Spent: 2 hours

## 5th of June

Today was highway call. today was cool because I finaly figured out a good way to make a turning system that I can implement into this.

I will add some more info later on it once I start thinking about it a bit more

Yeah i have no clue on how to do this.\
I wanna die\
why is this so difficult to figure out\
ooh wait\
new idea\
lemme make some sketches

Time spent: 30 mins

## 18th of June

okay I am gonna do a full redesign. Now it will use 4 motors(1 per wheel) so then turning will be a lot easier to figure out.

## 6th of June

New idea maybe works\
not known for sure\
but there is a chance

## 1st July

Damn i havent worked on this in a while.

Okay so Im just going to full send on the 4 motor idea since i cant figure out a way to reliably steer. I also redownloaded macos so i got shapr3d back and am gonna port everything over to there.

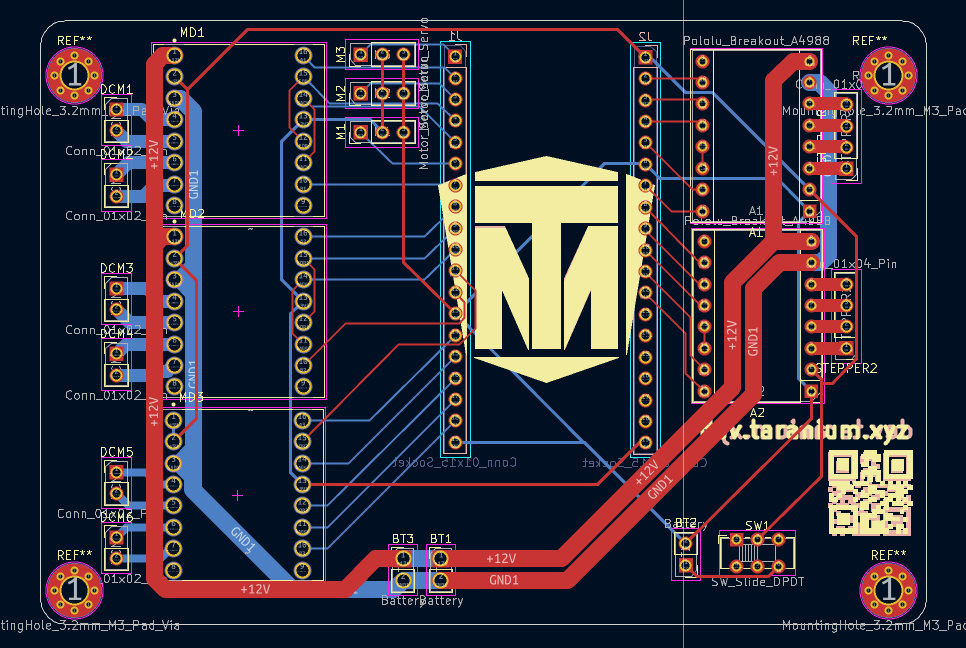
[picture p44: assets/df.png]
dsd


So today I redesigned the whole PCB(again) so now it can support all the motors I need and still have upgradeability and whatnot. I spent a while on this trying to make it have minimal vias(we dont like vias) and getting everything to line up well. th motor driver is a TB6612. its really nice and cool.

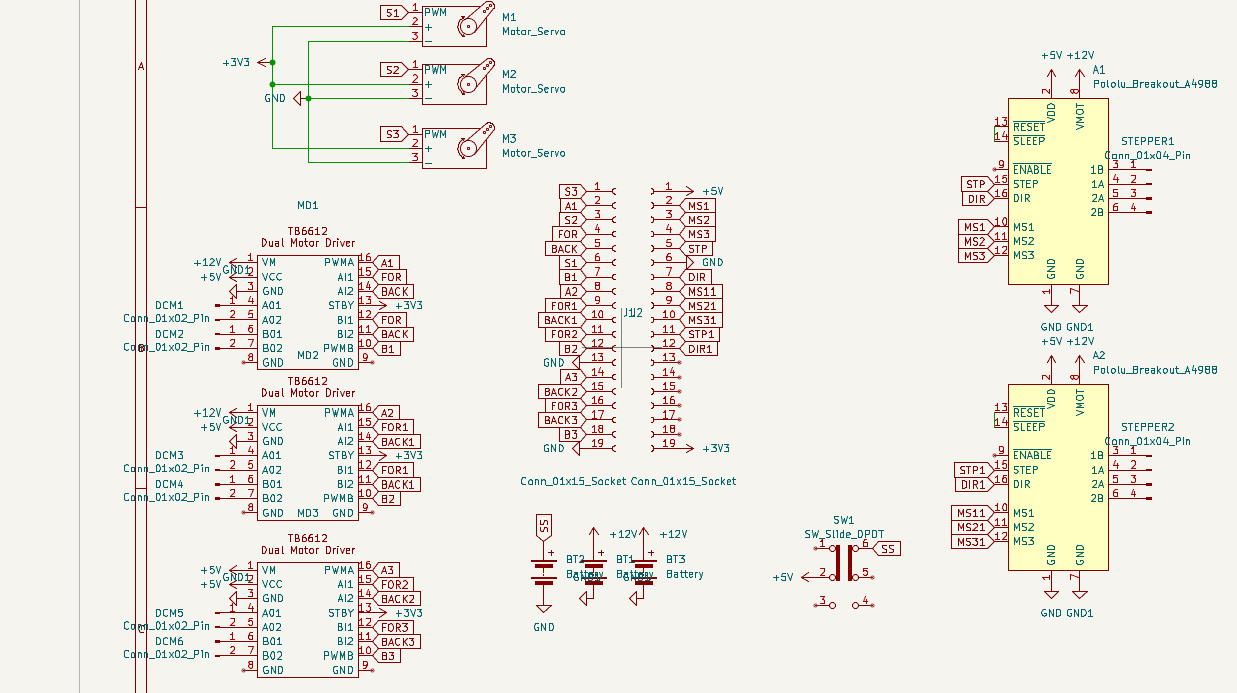
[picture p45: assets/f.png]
gfd


Oh and I made that symbol for the TB6612 btw. i wanted to make the footprint but i couldnt find any proper dimentions for it so i just pulled one off the internet

its crazy what this pcb used to be. but sadly i dont think anything else is possible.

time spent: 8 hours

## 2nd July

Time to start doing work on the model :D

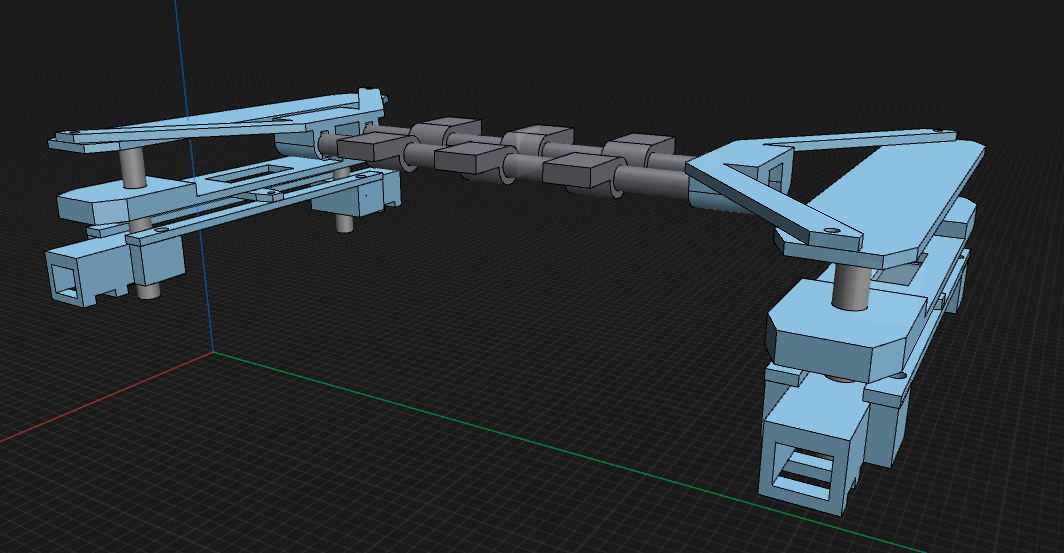
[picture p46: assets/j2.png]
hi


I fixed the motor mounts to actually rotate around a centre axle unlike before. and now it also has the screw holes and heatset holes fixed from 3mm and 5mm to 3.3 and 4.7 cuz i had it wrong  before.

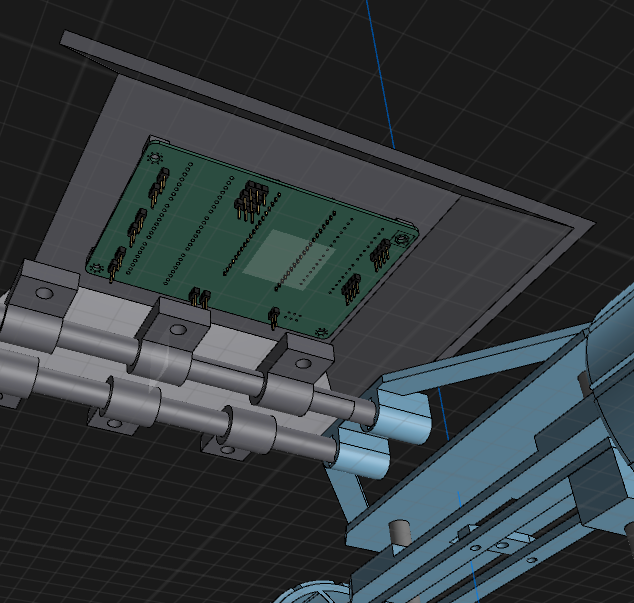
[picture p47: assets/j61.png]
b


I also started on the chasis since internals needed it in order to progress.

i start with a top shell and position it roughly how high I want the chasis to be from the Internals. I also noticed it was a pretty big surface so im gonna use that area and mount the pcb there because yes.

Total Time: 3 hours

## 6th July

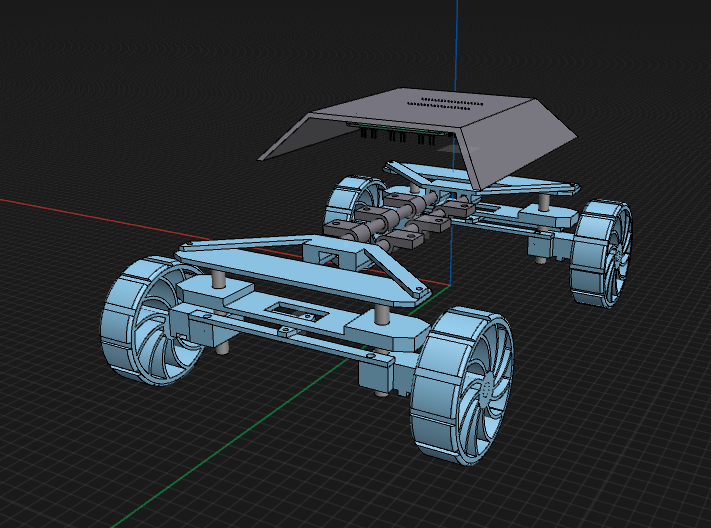
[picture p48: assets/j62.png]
djh


hi

I imported the wheels into the model and did some touch ups to the internals. little clean up stuff.

i also started chasis stuffs but more of it.

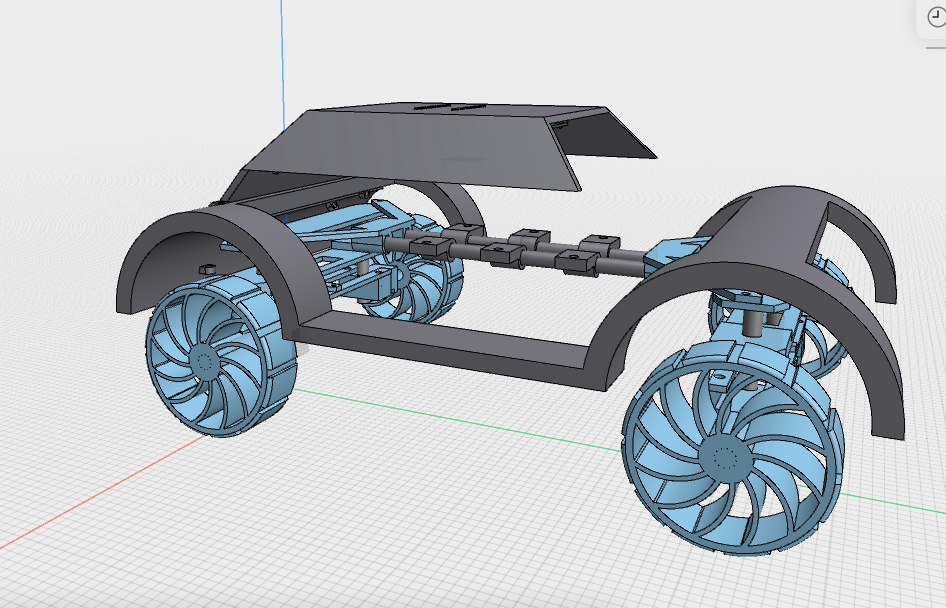
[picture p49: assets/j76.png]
d


I started making the wheel cover thingy for the car and connected them together to make a frame was pretty simple stuff but then i relise. i need wire management

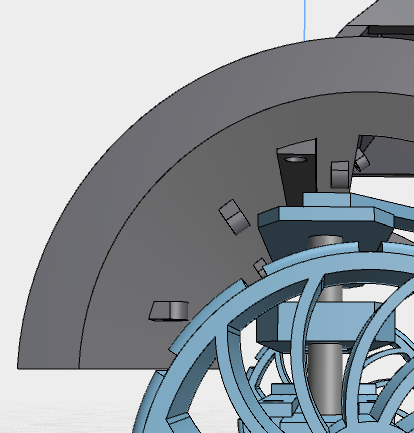
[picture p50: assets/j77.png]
sjhfg


So i made these little hook circle thingies. they dont hold wires by themselves. instead they were made to hold zip ties and you zip tie the wires to them.

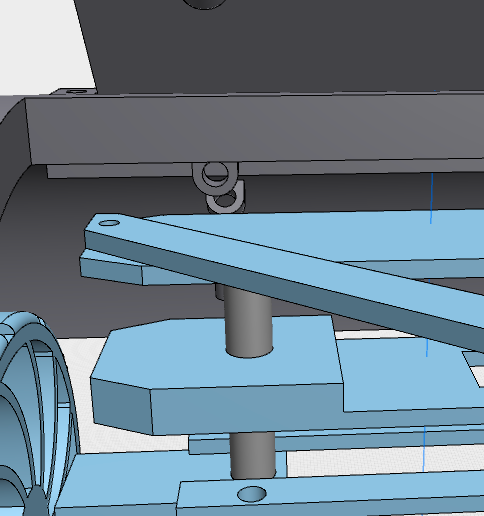
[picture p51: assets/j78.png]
fsjkhd


Better image^\
making these i just made one of them in a differnt place, moved it where i wanted it and then started copy pasting them where i wanted. pretty relaxing after the pain of doing chsis stuff.(it was easy but painful).

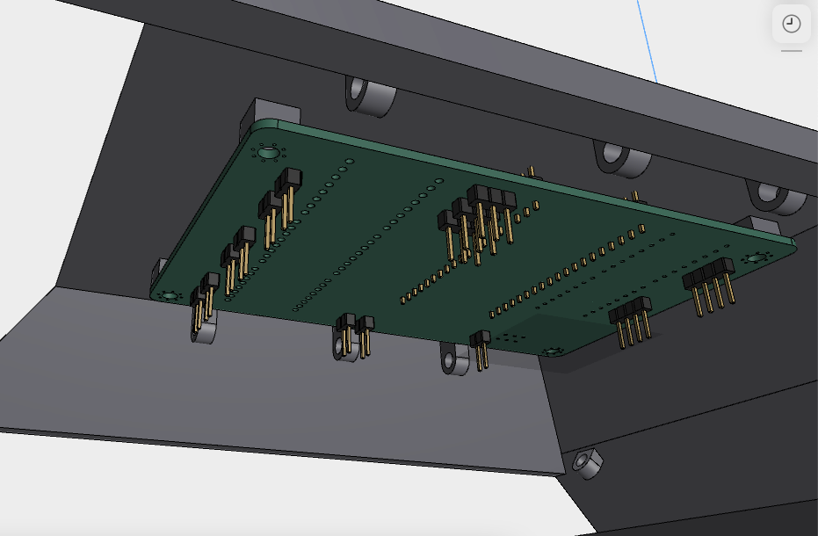
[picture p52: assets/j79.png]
gfs


The holes go all the way to the mainboard to wherenver they connect. pretty nice system if you ask me.

Time spent: 4 hr

## 7th July

hihi

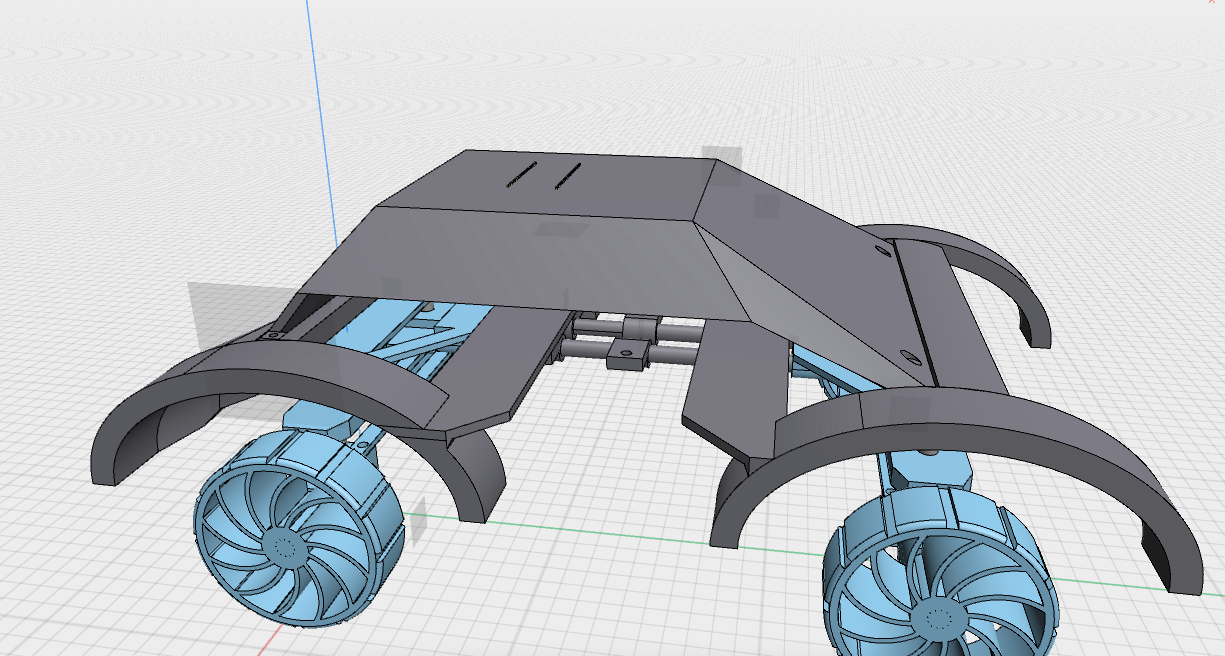
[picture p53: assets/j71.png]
hfgh


So i kinda messed up o the chasis design on lots of different areas so gonna talk about it here.\
So this is what the main chasis will look like. or at least this is the start of it.\
i did this design because I was just trying to make something car shaped and landed on this.\
anyways time to explain each part in depth.

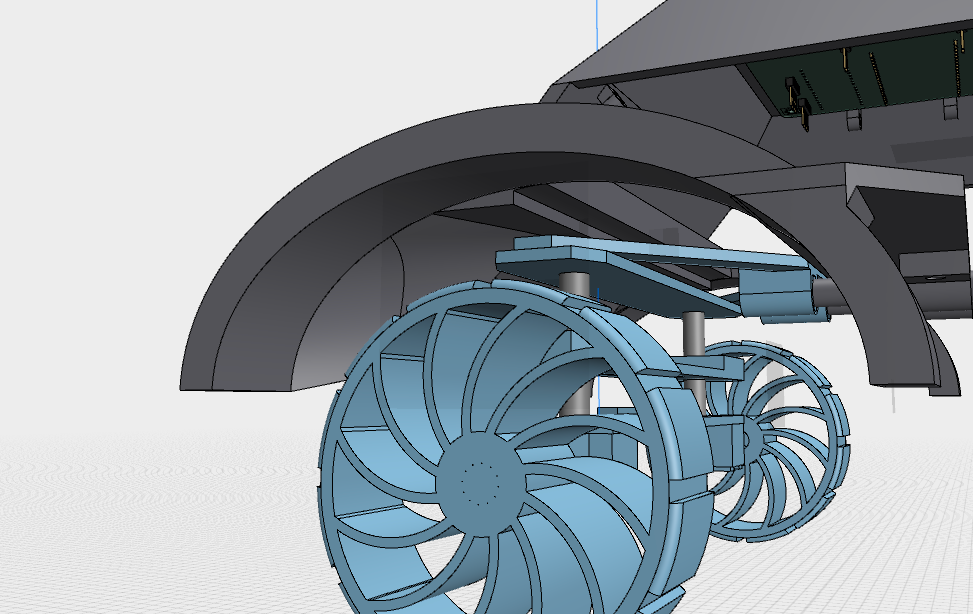
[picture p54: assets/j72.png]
gfdg


this is the tires cover/mudflap/idk im not a car person

either way its cool. I chose an oval because this thing needs to turn and the axis of rotation is fairly far away from the wheel itself which would mean thw it has lots of horizontal movement, therfore needing the extra space on the front and back

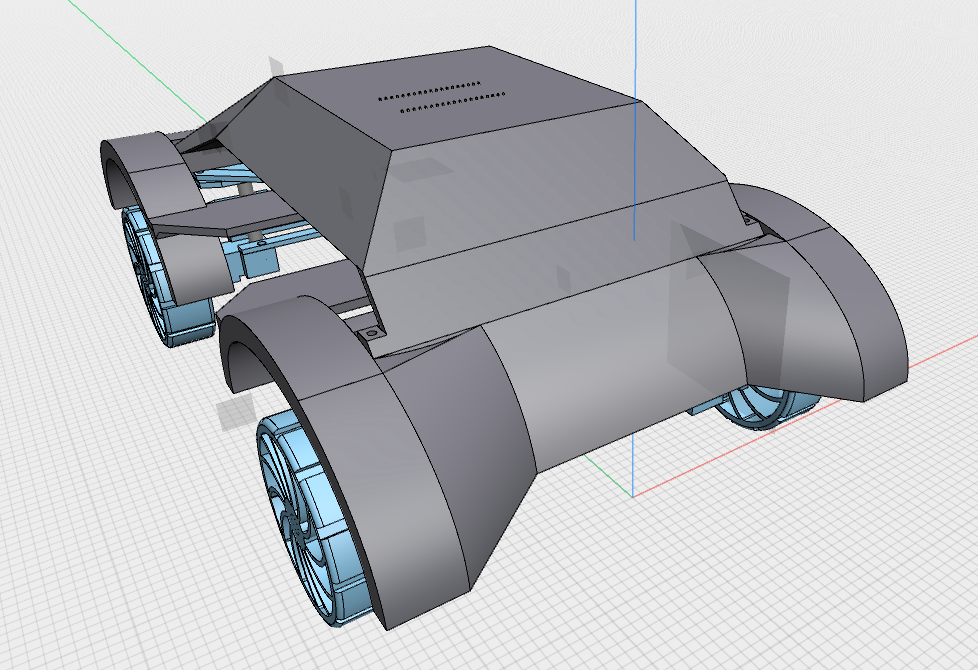
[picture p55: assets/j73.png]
dsk


This side actually looks good though\
you have to admit it\
I had lots of fun and pain with the loft and split body tools to make this with heaps of different sketches and shapes. to make this you are basically just making a bunch of planes and sketches and lofting them together. then use split body to remove excess materials

you can probably see way too many screw holes which will be a pain to build.

Also im ditching the arm now too. this thing is already really big and heavy. an arm would make that worse plus power comsumption would be through the roof. and i cant fit a bigger battery.

Time Spent: 5 hours

## 8th  july

nearly done

The top piece of the chasis is too big for my printer so i needed to chop it

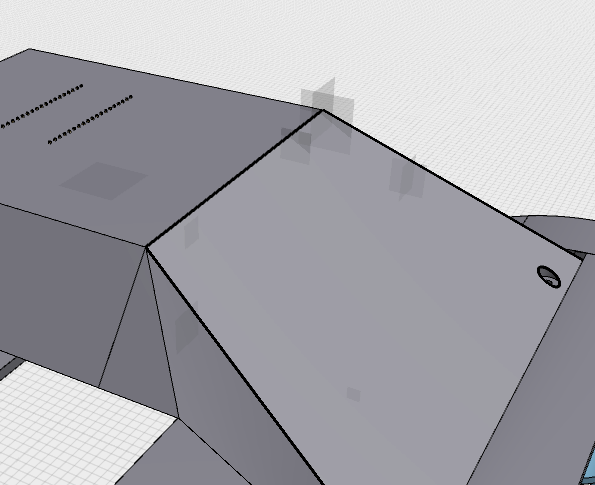
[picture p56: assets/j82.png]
fdgg


I made vertical cut here to split it into 2 pieces and added holes and a connector piece to seal it together.

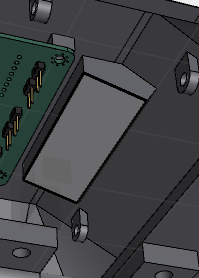
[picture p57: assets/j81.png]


this piece just has 4 screws go into it to connect those 2 pieces.

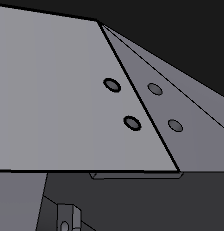
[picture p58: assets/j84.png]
fsdfsjf


I added the same bracket thing on the sides and  it looked pretty good. now it fots on my printer and works well(maybe)

Time Spent: 4 hours

## 9th july

Time to work on battery mount. Final straw( I think)

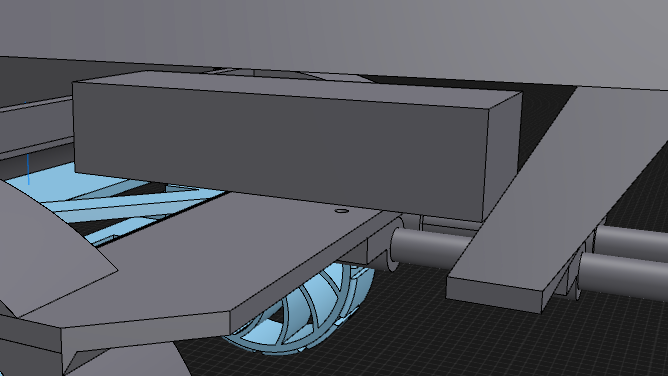
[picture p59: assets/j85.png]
gsf


so this is how big the battery is. takes up a decent chunk of size and now i gotta make a braket for it.

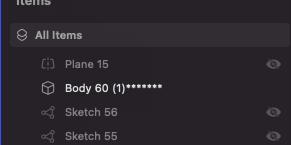
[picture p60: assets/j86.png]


before we start, funny number

I changed the colurs of the cad to some I think that I would like so the following may be a bit hard to see.

gddfgkdf

Here is what the completed bracket looks like.

I basically just made a box around the battery and made a J that goes over the battery and uses screws to hold itself in. You can also see the connector piece from earlier. I multitasked it to also act as a support beam for the front and to connect the chasis to the frame. pretty cool.

Time Spent: 6 hours

## 19th of July

Okay I need to speedrun this project if I want it out on time to get my stipends.

so controller time. I speedrun this so fast in one day. 

First what i wanted: 2 encoders, 2 triggers, all battery powered.

Here are images of what I made:

sfd

dsfs

This is the controller. it uses 2 horizontal encoders. (one for acceleration, other for turning.

trigger 1 changes driection, trigger 2 just exists for now until i decide what to do with it.

for the joysticks on the encoders, i used a bunch of drafts to get a general shape and then filleted a bunch to get the curves. the this is that there was no feasable wayt ot get it into the case to begin with so i chopped off the top and gave it a rod so it can be assembled.

sfd

the pcb schematic looks like so:

sfsdf

the extra battery stuff is for a boost converter since the esp needs 5V and not 3.7 that normal lipos give.

The LED and resistor is an indicator led to tell when it is on. it would make a low underglow from the case. i can adjust the resistance to make it lower glow if nessasary.

time spent: 8 hours

## 20th of July

Okay time to start submission stuffs
need to make a readme and luckily i made my bom while working of ts

It got rejected :(

## 29th of July

Okay every other project is done. now to speed run changes here

FIRSt i need to downgrade from 4wd to to 2wd, next create a gear down systenm and new turning system that is stronger than the previous one.

then new pcb to accomodate stronger motors

and new firmware

okay so first grinding the model

adfds

here is what i had before for my turning

i need to change it to 2 separate systems. this will let me do differential turning

It needs to be stronger + needs to be 2 separate servos + more stability

I spent a bit on it and got this thingy up:

fdws

Hours spent: 3

## 30th july

okay full sprint time

so made a gear system in onshape and made brackets and whatnot. it will be 16:1 

sdffsdf

spent like 4 hours on this because of how iffy gears are

I went through liek a bunch of different ratios and combos to see which one would fit the best and landed on this.

so thats nice. imma finish turning system now

fsdfs

okay thats done. imma use dowels to hold the parts together because its better than screws

okay problem with the gears. 

the motors can't go next to each other without clipping 

sdfsdf

I need to extend it out by at least 40mm to make it fit sure one wheel would need to spin a bit slowwr but I can fix that in firmware

it should be fine hopefully.

I spent a while looking at alternatives for the motor but I couldn't really find anything that was strong enough.

time spent: 8 hours

## 31st of July 

wait a minut

I think i put the gears on backwards

imma kms

holy fjdwfgjsaklgfjqsfagf
s

how am i so dumb

okay time to fix this

*one eternity later*

fwdfsf

okay so i changed it to be the right way round this time

so now it makes the motor slower instead of faster

okay so because I was given the opportunity to change the gears up a little, I used it to add anti slip to the gear(probably should have done the a while ago) but also make the gears go outwards a bit instead of staying in a line. so now I can get my 2 motors to fit together on a single line. 

okay tbh I did the extending thing first and then I had the vision to do it like that and it worked so me happy.

sdfsdf

Next I need to do the PCB. I need to use the BTS7960 motor driver. because tb6612 doesn't have enough current for the 775s(new stronger motor)

this thing is mounted separately off the PCB. and has 8 wires that connect to the microcontroller 

each one controlls one motor so I need 2 of these. 

so I put 2 2x4 headers on my PCB and connected it based on the AliExpress product description.

this made my PCB shorter. which was nice.

also amongus

fgdg

okay now I need to update my model based on the new PCB and to handle new drivers that need to be mounted.

I spent like an hour doing different ways to position the 3 PCBs to mount it( mainly waiting cuz my laptop is getting Hella slow and the file is getting really big atp.

I eventually got it

it's really really tight though.

so after that I sent the model in for a sanity check in #highway and they pointed out a few things. my motor mount wasn't connected to anything, and the turning main rod looked weak.

so I fixed the mount problem and slept

Time spent: 12 hours :sob:

## 1st August 

time to grind in school 

fixed the turning issue thingy being weak in about an hour

fsdsf

then started doing final touches and taking screenshots /renders of everything for the readme

after that I did a small amount of BOM stuff but my 3rd class didn't have much room to do stuff

I spent about 3 and a half hours at school working

and then got the BOM and readme done

I went to the library and spent like 20 mins doing firmware and finished BOM

time spent:4 hours

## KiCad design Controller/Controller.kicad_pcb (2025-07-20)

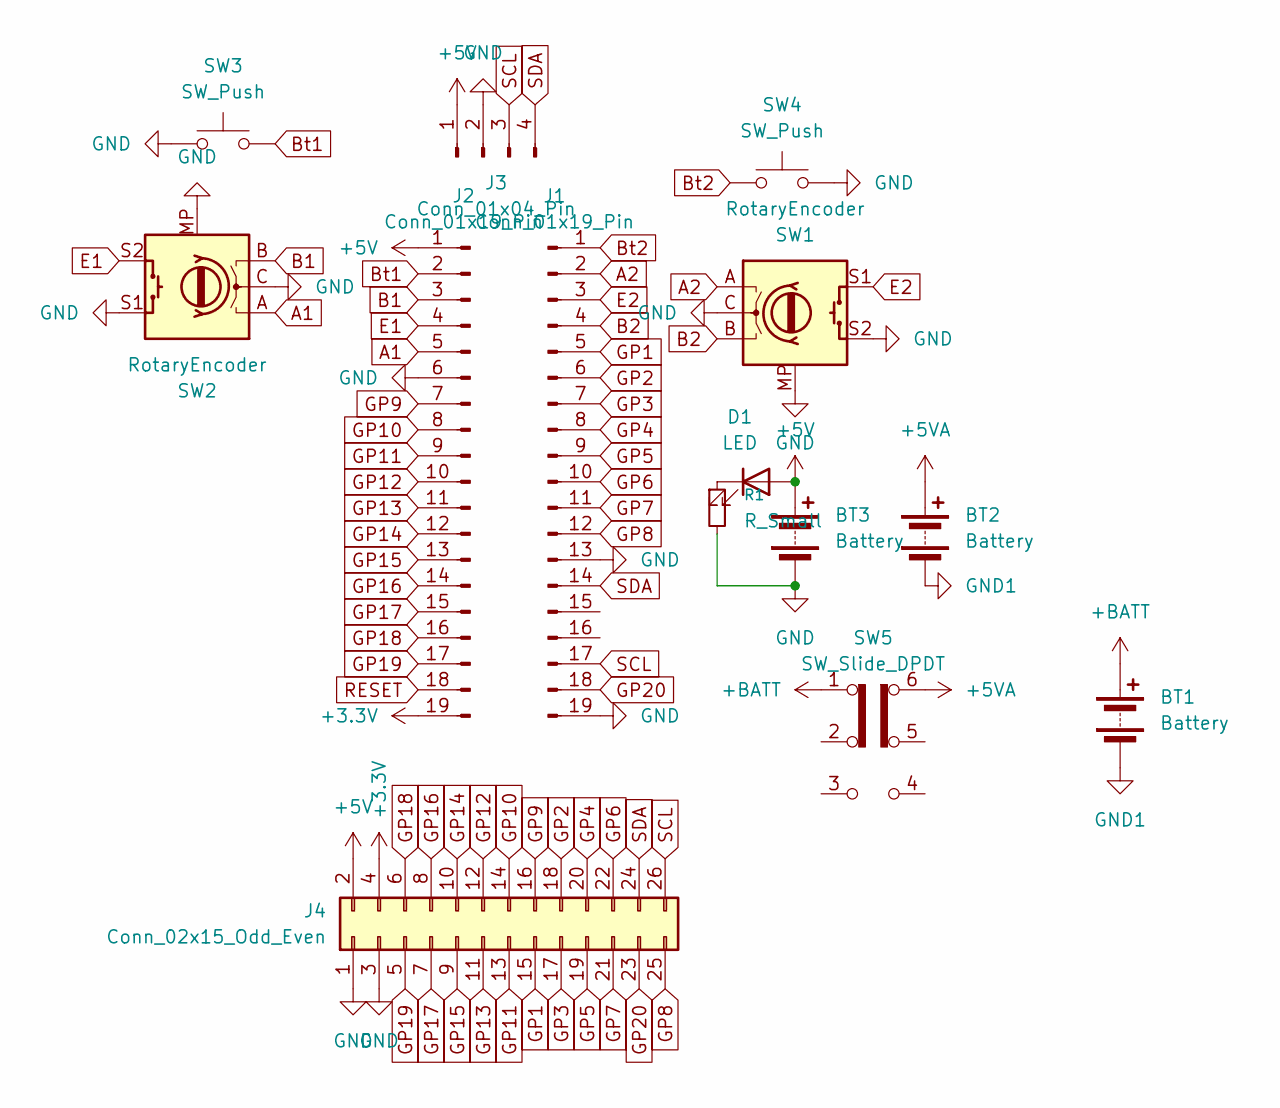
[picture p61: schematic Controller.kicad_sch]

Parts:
BT1: Battery; JST_XH_B2B-XH-A_1x02_P2.50mm_Vertical
BT2, BT3: Battery; PinSocket_1x02_P2.54mm_Vertical
D1: LED; LED_D3.0mm
J1, J2: Conn_01x19_Pin; PinSocket_1x19_P2.54mm_Vertical
J3: Conn_01x04_Pin; MODULE_DM-OLED096-636
J4: Conn_02x15_Odd_Even; PinHeader_2x13_P2.54mm_Vertical
R1: R_Small; R_Axial_DIN0204_L3.6mm_D1.6mm_P5.08mm_Horizontal
SW1, SW2: RotaryEncoder; EC11-Horizontal
SW3, SW4: SW_Push; Button-6mm-2pin-tht
SW5: SW_Slide_DPDT; SW_E-Switch_EG1271_SPDT

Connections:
+3.3V: J2.19, J4.4
+5V: BT3.1 (+), D1.2 (A), J2.1, J3.1, J4.2
+5VA: BT2.1 (+), SW5.6 (C)
+BATT: BT1.1 (+), SW5.1 (A)
A1: J2.5, SW2.A
A2: J1.2, SW1.A
B1: J2.3, SW2.B
B2: J1.4, SW1.B
Bt1: J2.2, SW3.2
Bt2: J1.1, SW4.1
E1: J2.4, SW2.S2
E2: J1.3, SW1.S1
GND: BT3.2 (-), J1.13, J1.19, J2.6, J3.2, J4.1, J4.3, R1.2, SW1.C, SW1.MP, SW1.S2, SW2.C, SW2.MP, SW2.S1, SW3.1, SW4.2
GND1: BT1.2 (-), BT2.2 (-)
GP1: J1.5, J4.15
GP2: J1.6, J4.18
GP3: J1.7, J4.17
GP4: J1.8, J4.20
GP5: J1.9, J4.19
GP6: J1.10, J4.22
GP7: J1.11, J4.21
GP8: J1.12, J4.25
GP9: J2.7, J4.16
GP10: J2.8, J4.14
GP11: J2.9, J4.13
GP12: J2.10, J4.12
GP13: J2.11, J4.11
GP14: J2.12, J4.10
GP15: J2.13, J4.9
GP16: J2.14, J4.8
GP17: J2.15, J4.7
GP18: J2.16, J4.6
GP19: J2.17, J4.5
GP20: J1.18, J4.23
unnamed: D1.1 (K), R1.1
RESET: J2.18
SCL: J1.17, J3.3, J4.26
SDA: J1.14, J3.4, J4.24

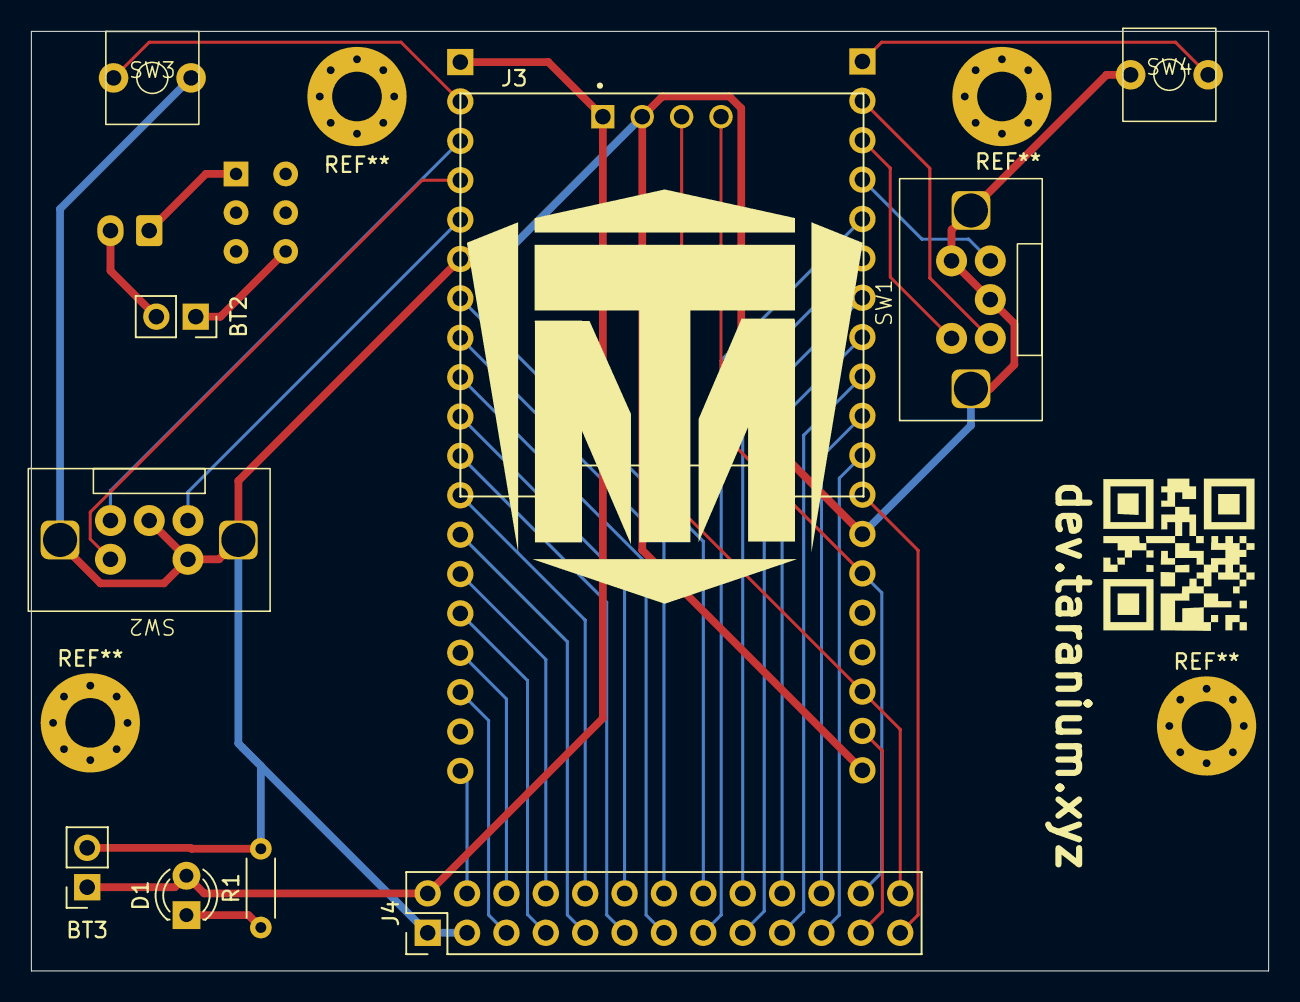
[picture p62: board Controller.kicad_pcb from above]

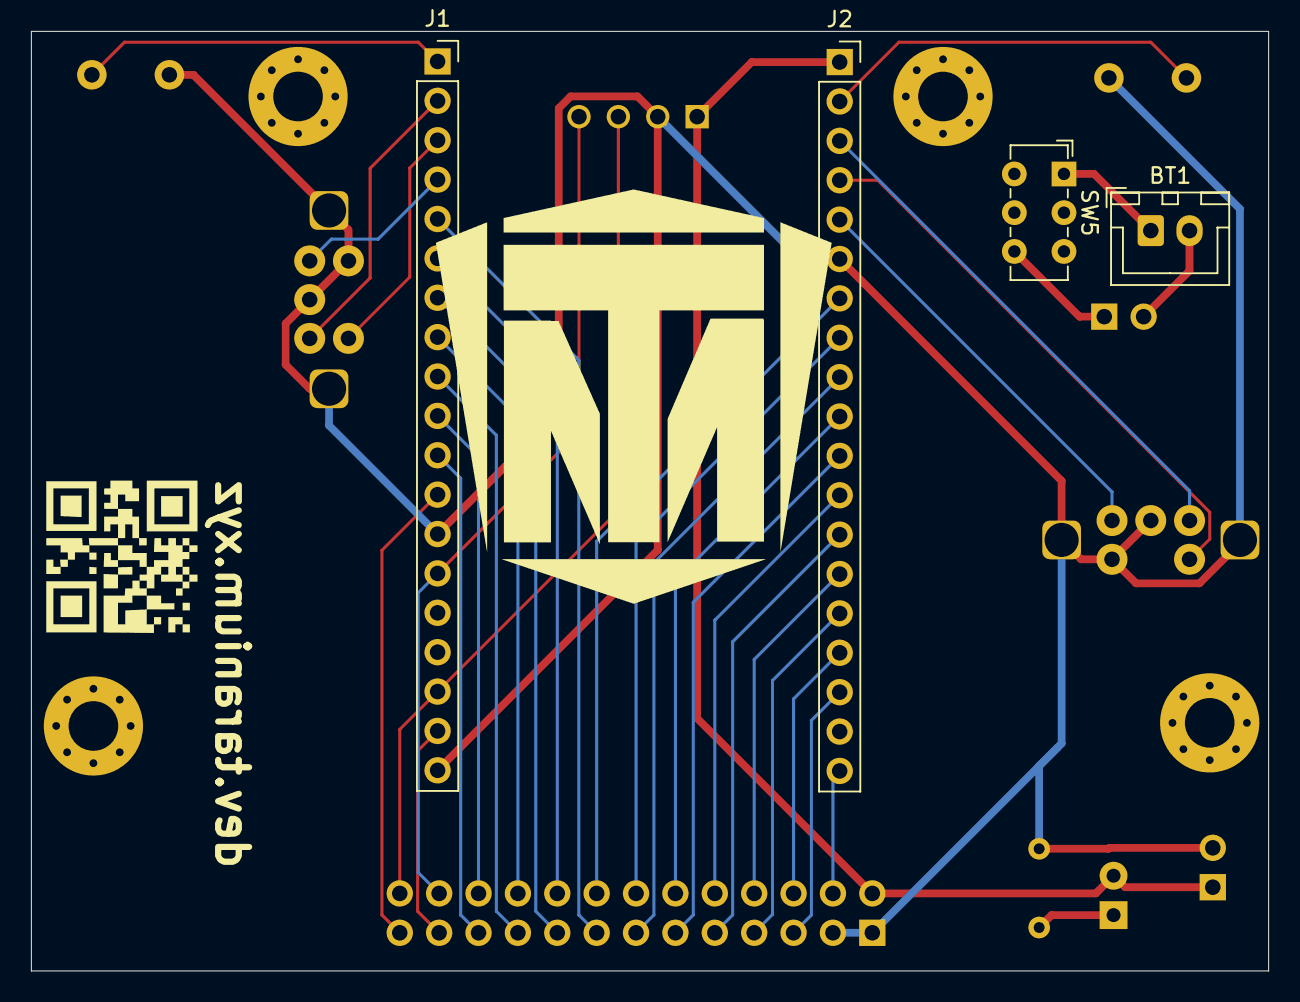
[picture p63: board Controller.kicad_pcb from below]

Board: 2 copper layers, 79.8 x 60.6 mm, 14 parts (4 on the bottom side), 37 nets.

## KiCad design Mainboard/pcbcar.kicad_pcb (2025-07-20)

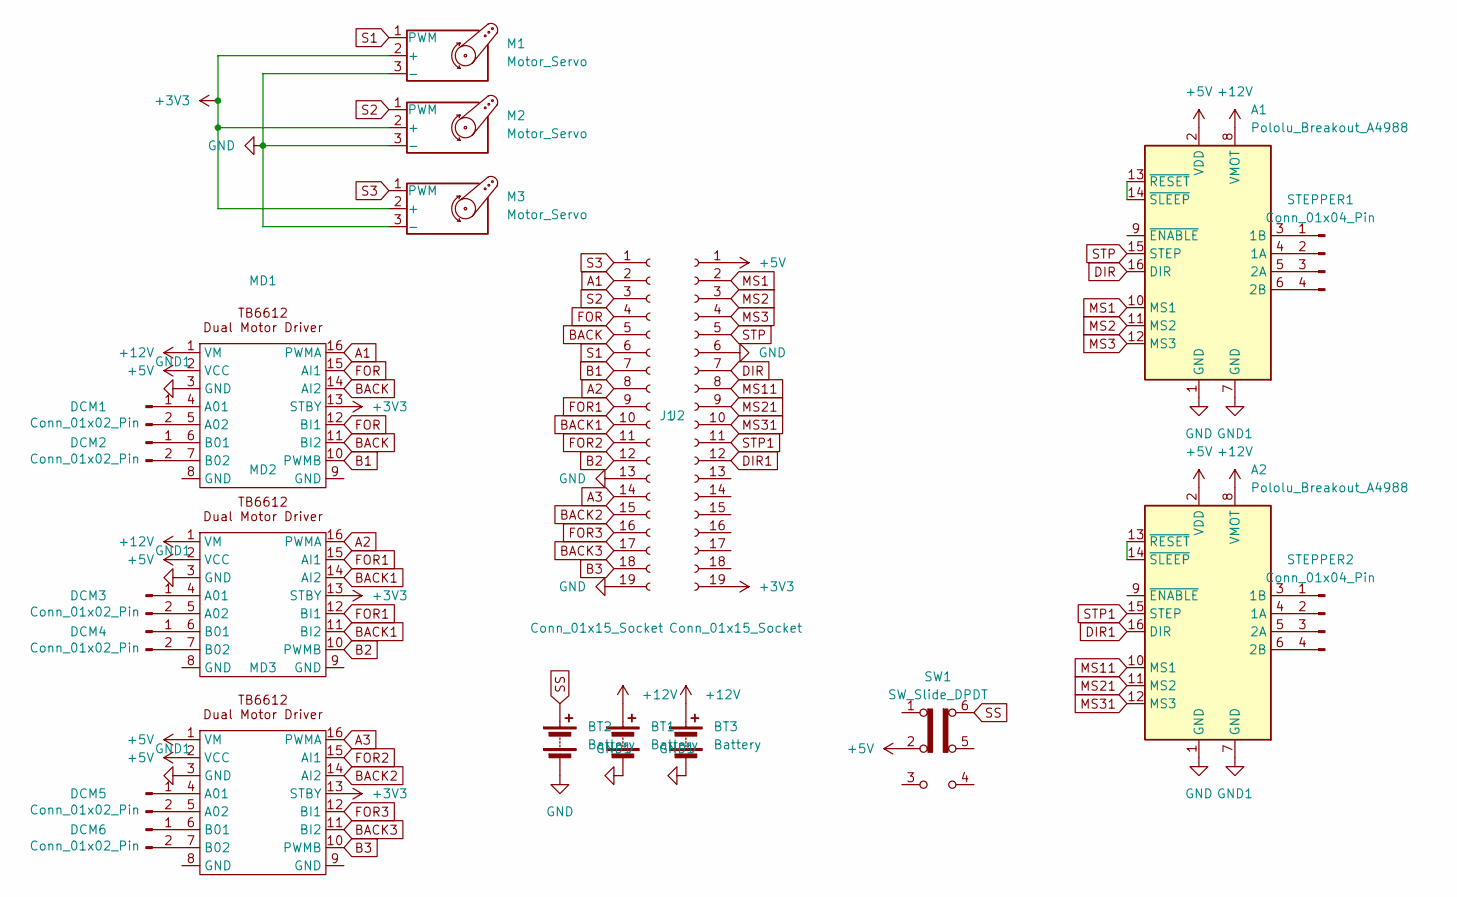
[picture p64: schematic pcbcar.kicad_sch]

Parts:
A1, A2: Pololu_Breakout_A4988; Pololu_Breakout-16_15.2x20.3mm
BT1, BT2, BT3: Battery; PinHeader_1x02_P2.54mm_Vertical
DCM1, DCM2, DCM3, DCM4, DCM5, DCM6: Conn_01x02_Pin; PinHeader_1x02_P2.54mm_Vertical
J1, J2: Conn_01x15_Socket; PinHeader_1x19_P2.54mm_Vertical
M1, M2, M3: Motor_Servo; PinHeader_1x03_P2.54mm_Vertical
MD1, MD2, MD3: MODULE_ROB-14450
STEPPER1, STEPPER2: Conn_01x04_Pin; PinHeader_1x04_P2.54mm_Vertical
SW1: SW_Slide_DPDT; SW_E-Switch_EG1271_SPDT

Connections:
+3V3: J2.19, M1.2 (+), M2.2 (+), M3.2 (+), MD1.13 (STBY), MD2.13 (STBY), MD3.13 (STBY)
+5V: A1.2 (VDD), A2.2 (VDD), J2.1, MD1.2 (VCC), MD2.2 (VCC), MD3.1 (VM), MD3.2 (VCC), SW1.2 (B)
+12V: A1.8 (VMOT), A2.8 (VMOT), BT1.1 (+), BT3.1 (+), MD1.1 (VM), MD2.1 (VM)
A1: J1.2, MD1.16 (PWMA)
A2: J1.8, MD2.16 (PWMA)
A3: J1.14, MD3.16 (PWMA)
B1: J1.7, MD1.10 (PWMB)
B2: J1.12, MD2.10 (PWMB)
B3: J1.18, MD3.10 (PWMB)
BACK: J1.5, MD1.11 (BI2), MD1.14 (AI2)
BACK1: J1.10, MD2.11 (BI2), MD2.14 (AI2)
BACK2: J1.15, MD3.14 (AI2)
BACK3: J1.17, MD3.11 (BI2)
DIR: A1.16 (DIR), J2.7
DIR1: A2.16 (DIR), J2.12
FOR: J1.4, MD1.12 (BI1), MD1.15 (AI1)
FOR1: J1.9, MD2.12 (BI1), MD2.15 (AI1)
FOR2: J1.11, MD3.15 (AI1)
FOR3: J1.16, MD3.12 (BI1)
GND: A1.1 (GND), A2.1 (GND), BT2.2 (-), J1.13, J1.19, J2.6, M1.3 (-), M2.3 (-), M3.3 (-)
GND1: A1.7 (GND), A2.7 (GND), BT1.2 (-), BT3.2 (-), MD1.3 (GND), MD2.3 (GND), MD3.3 (GND)
MS1: A1.10 (MS1), J2.2
MS2: A1.11 (MS2), J2.3
MS3: A1.12 (MS3), J2.4
MS11: A2.10 (MS1), J2.8
MS21: A2.11 (MS2), J2.9
MS31: A2.12 (MS3), J2.10
unnamed: A1.4 (1A), STEPPER1.2
unnamed: A1.3 (1B), STEPPER1.1
unnamed: A1.5 (2A), STEPPER1.3
unnamed: A1.6 (2B), STEPPER1.4
unnamed: A1.13 (~RESET), A1.14 (~SLEEP)
unnamed: A2.4 (1A), STEPPER2.2
unnamed: A2.3 (1B), STEPPER2.1
unnamed: A2.5 (2A), STEPPER2.3
unnamed: A2.6 (2B), STEPPER2.4
unnamed: A2.13 (~RESET), A2.14 (~SLEEP)
unnamed: DCM1.1, MD1.4 (A01)
unnamed: DCM1.2, MD1.5 (A02)
unnamed: DCM2.1, MD1.6 (B01)
unnamed: DCM2.2, MD1.7 (B02)
unnamed: DCM3.1, MD2.4 (A01)
unnamed: DCM3.2, MD2.5 (A02)
unnamed: DCM4.1, MD2.6 (B01)
unnamed: DCM4.2, MD2.7 (B02)
unnamed: DCM5.1, MD3.4 (A01)
unnamed: DCM5.2, MD3.5 (A02)
unnamed: DCM6.1, MD3.6 (B01)
unnamed: DCM6.2, MD3.7 (B02)
S1: J1.6, M1.1 (PWM)
S2: J1.3, M2.1 (PWM)
S3: J1.1, M3.1 (PWM)
SS: BT2.1 (+), SW1.6 (C)
STP: A1.15 (STEP), J2.5
STP1: A2.15 (STEP), J2.11

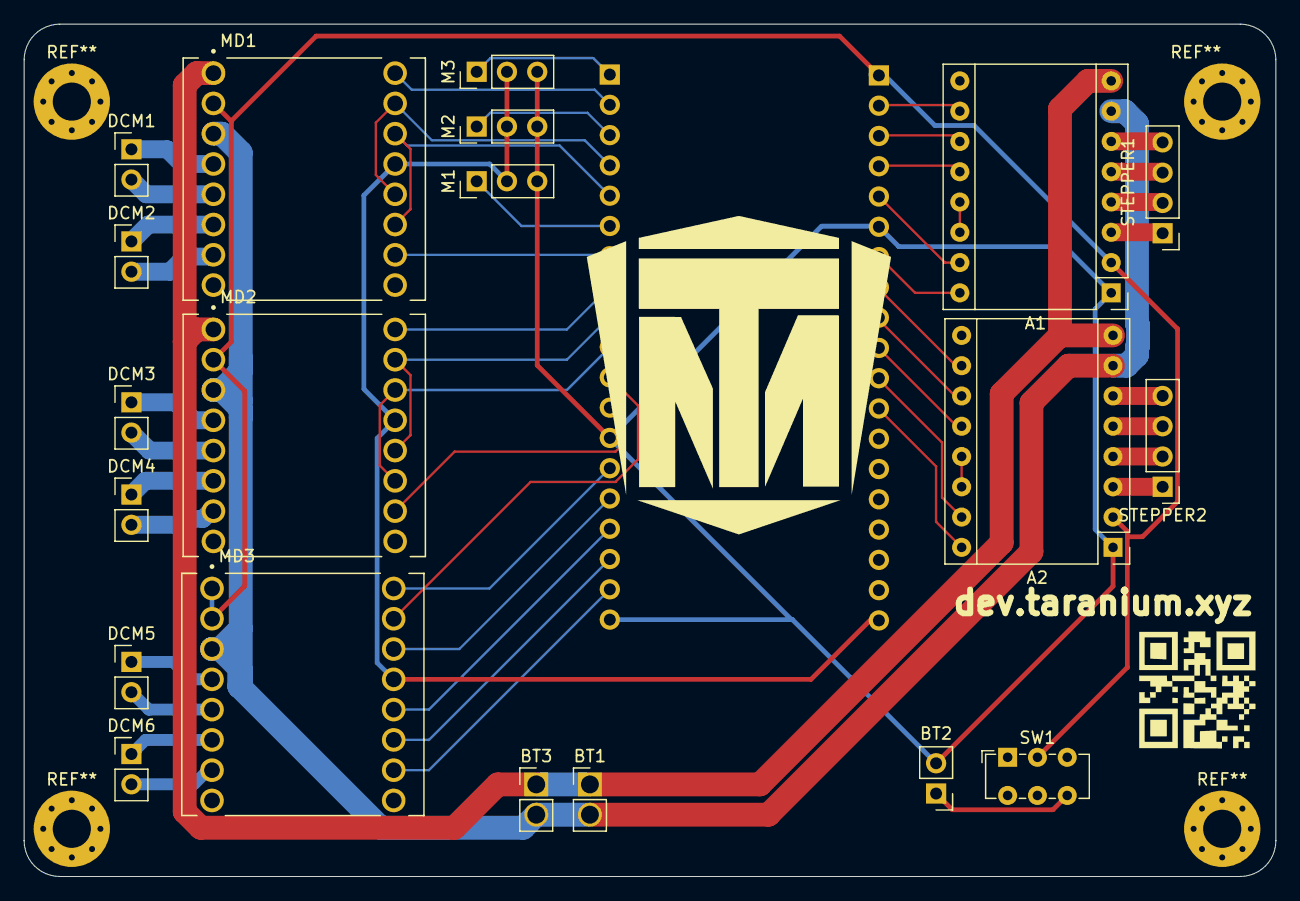
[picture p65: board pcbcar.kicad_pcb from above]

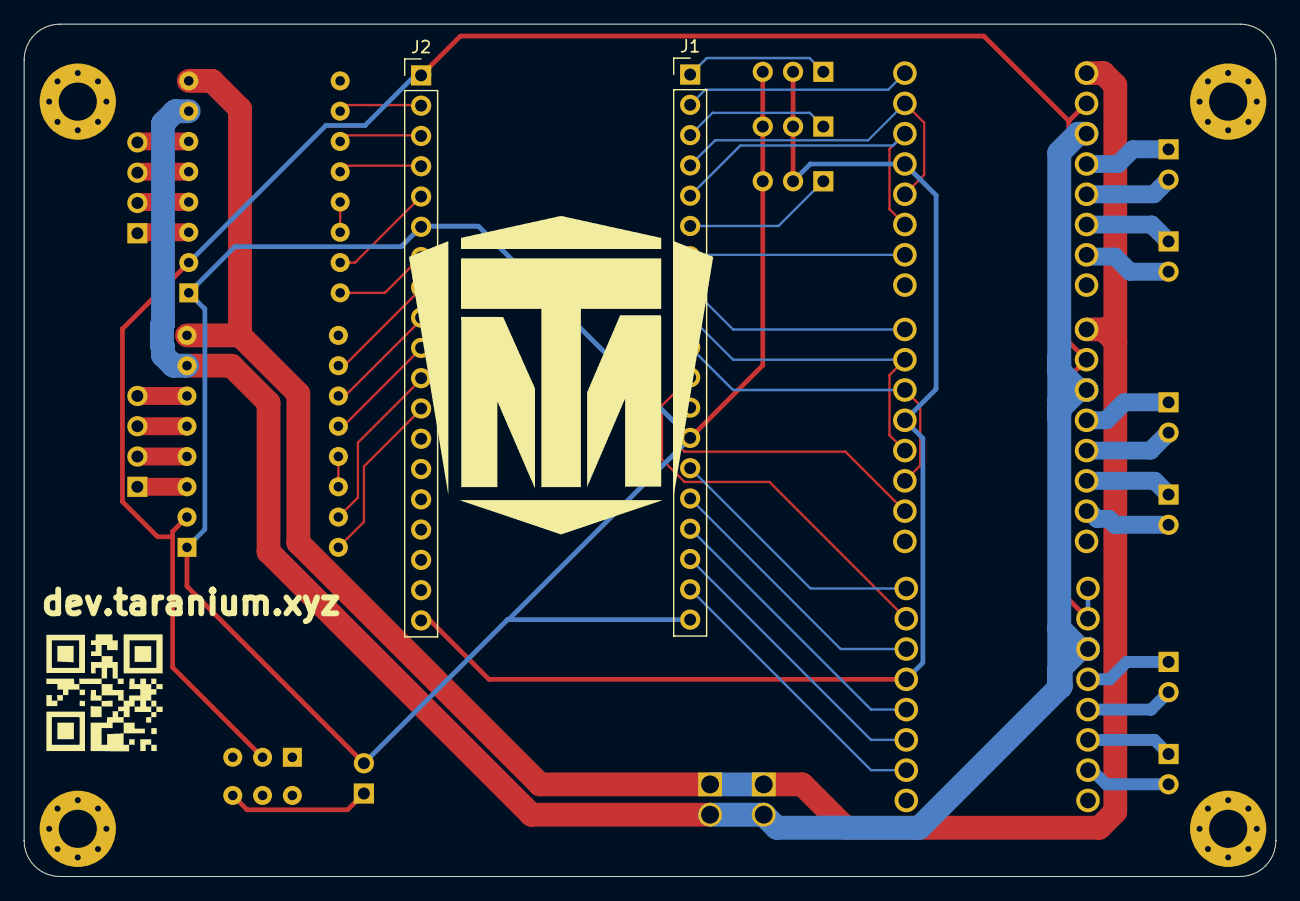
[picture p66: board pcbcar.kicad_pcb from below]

Board: 2 copper layers, 105.0 x 71.5 mm, 22 parts (2 on the bottom side), 55 nets.

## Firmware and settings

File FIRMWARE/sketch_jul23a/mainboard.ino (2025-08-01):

#define FrontFor 1
#define FrontBack 2
#define BackFor 3
#define BackBack 4

#define FrontS1 5
#define FrontS2 6
#define BackS1 7
#define BackS2 8

#define Servo1 9
#define Servo2 10
#define Servo3 11



void setup() {

  pinMode(FrontFor, OUTPUT);
  pinMode(FrontBack, OUTPUT);
  pinMode(BackFor, OUTPUT);
  pinMode(BackBack, OUTPUT);
  pinMode(FrontS1, OUTPUT);
  pinMode(FrontS2, OUTPUT);
  pinMode(BackS1, OUTPUT);
  pinMode(BackS2, OUTPUT);
  pinMode(Servo1, OUTPUT);
  pinMode(Servo2, OUTPUT);
  pinMode(Servo3, OUTPUT);
  interrupts();

}

void loop() {
  
  delay(1);
}

void LeftT() {
  if(digitalRead(Ltrigger)) {
    dir = !dir;
  }
}

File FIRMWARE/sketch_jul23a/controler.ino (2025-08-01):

#define LeftT 1
#define RightT 2

#define A1 3
#define B1 4
#define A2 5
#define B2 6

bool dir = 0;


void setup() {
  pinMode(LeftT, INPUT);
  pinMode(RightT, INPUT);
  pinMode(A1, INPUT);
  pinMode(B1, INPUT);
  pinMode(A2, INPUT);
  pinMode(B2, INPUT);
  interrupts();
}

void loop() {
  delay(1);
}

void Ltrigger() {
    dir = !dir;
}

void Rtrigger() {
    dir = !dir;
}
